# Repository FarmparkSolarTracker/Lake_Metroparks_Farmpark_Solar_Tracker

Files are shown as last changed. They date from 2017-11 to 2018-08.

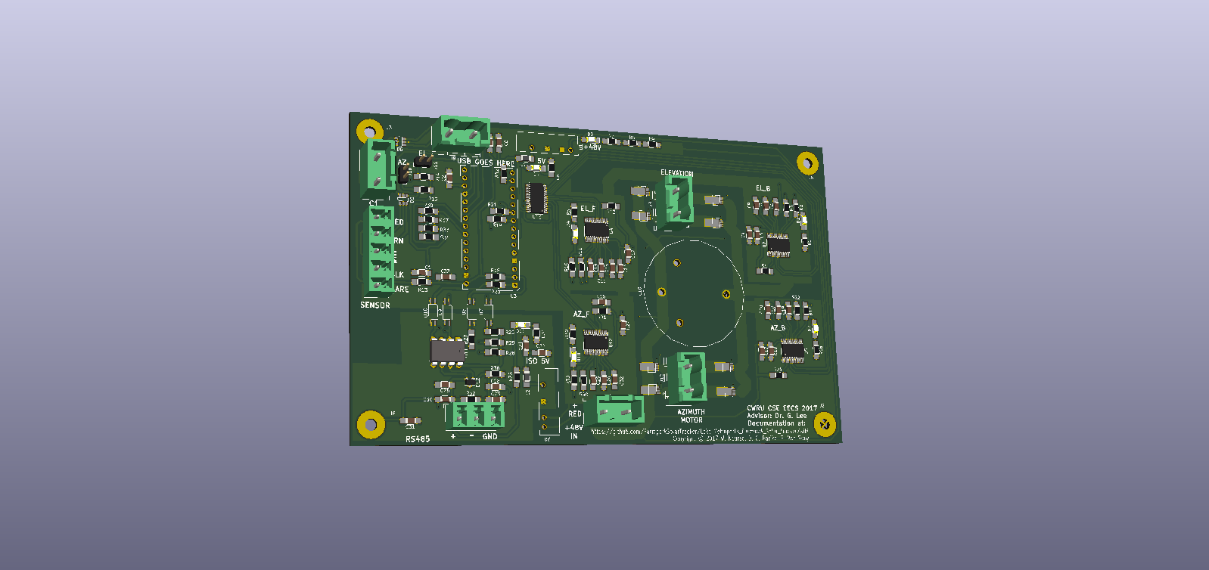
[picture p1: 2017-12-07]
Pictures/Solar_Tracker.png

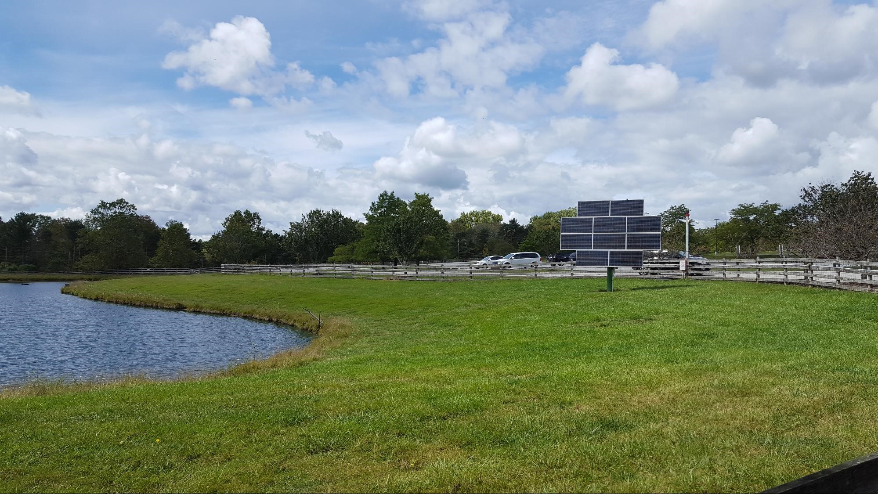
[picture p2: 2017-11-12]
Pictures/solar panel.jpg

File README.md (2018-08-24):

# Lake_Metroparks_Farmpark_Solar_Tracker
For more information, please see the wiki [here](https://github.com/FarmparkSolarTracker/Lake_Metroparks_Farmpark_Solar_Tracker/wiki).  

# Things which need work:
* Possible board issue where one side of the H-Bridges is unable to pull low, it only reaches High-Impedance
* Software for board is in a preliminary version, has not been fully tested due to the above issue
* A rough tester board has been included in the box, which theoretically can be used to send RS-485 commands to the main PCB. Code needs to be written for this device
* If the park has not done it yet, a new motor for the azimuth system must be ordered (it is believed that the worm gear is broken)
* The elevation linear actuator must be clamped in place
* Grommets must be put in place on the cables entering the new box
* Better data should be collected from the sensor, to better know how it operates

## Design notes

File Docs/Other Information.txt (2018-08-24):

Wattsun Contact Information:
	-The panel/installation model is the AZ-120
	-The two people at Watt-sun to contact are:
		-Jeff: (976)476-1256
		-Kyle: (973)647-7751
	-A replacement motor unit for the Azimuth unit was quoted to be $235, plus shipping

Drive Information:
	-I had difficulty getting the timing of the PWM expander to work with driving both the top and bottom
	of each H-Bridge, so the compromise I reached was that the bottom mosfet of the H-bridge on the appropriate
	side is held on for the duration of motion, and the corresponding top transistor is PWMed to control the 
	speed/voltage of the motor.

Preliminary Light Sensor Data:
	SIDE OF SENSOR FACING SUN | WHITE WIRE ADC | GREEN WIRE ADC
	-----------------------------------------------------------
	Middle					  | 1023           | 1023
	-----------------------------------------------------------
	Right					  | 0              | 1023
	-----------------------------------------------------------
	Left                      | 1000           | 300
	-----------------------------------------------------------
	Top                       | 600            | 1000
	-----------------------------------------------------------
	Bottom                    | 1000           | 0

Sensor schematic/pinout
	-Red: +5v in (needs a current limiting resistor)
	-Green: Middle of 2 photodiodes
	-White: Middle of other 2 photodiodes
	-Black: Ground
	-Bare: Ground for shielding

	 -------------------------------------------O +5v
	 |             |                    
	 |             | 
	___           ___
	\_/           \_/
	---           ---
	 |             |
	 |             |____________________________O Green
	 |             |                              
	 |_____________|____________________________O White
	 |             |                    
	 |             | 
	___           ___
	\_/           \_/
	---           ---
	 |             |
	 -------------------------------------------O Black

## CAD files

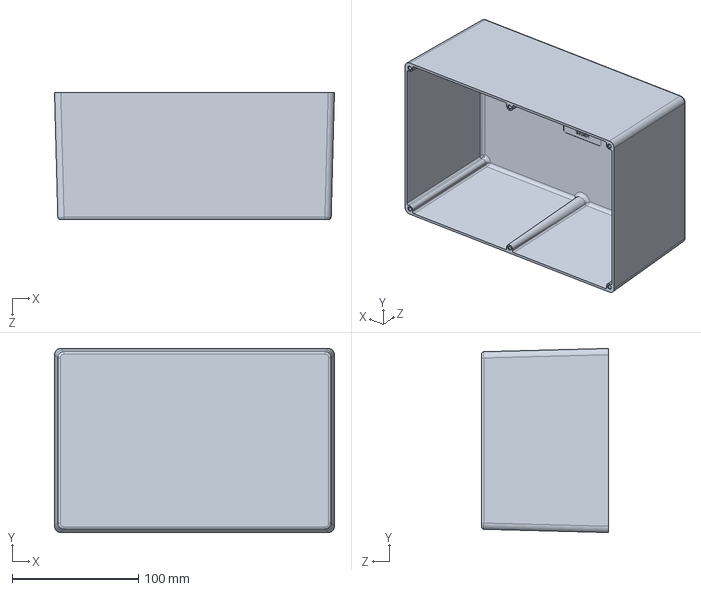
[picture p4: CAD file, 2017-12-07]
SOLIDWORKS/HM-1220-ND Box.SLDPRT
222.0 x 146.0 x 101.0 mm

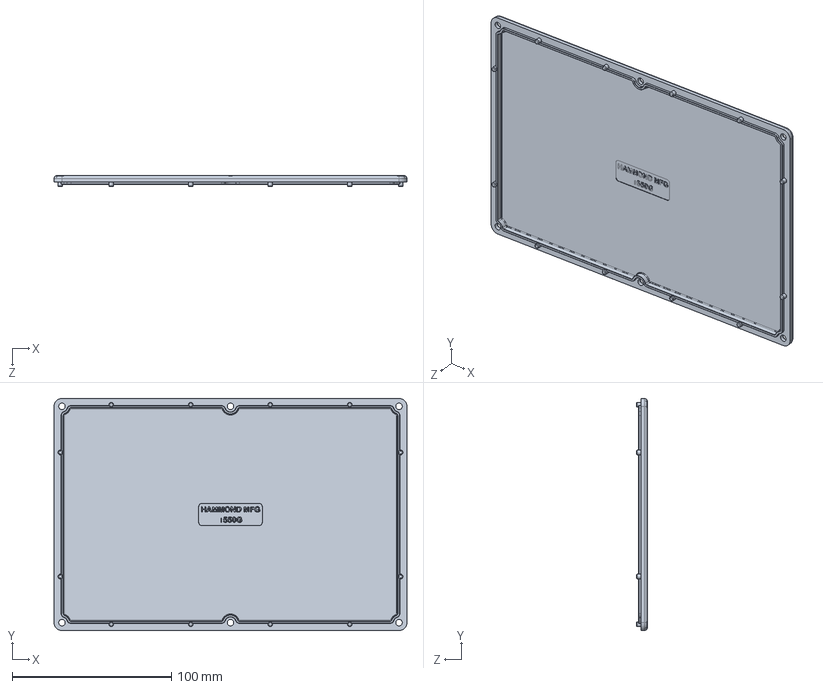
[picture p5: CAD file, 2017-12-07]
SOLIDWORKS/HM-1220-ND Lid.SLDPRT
222.0 x 146.0 x 7.00 mm

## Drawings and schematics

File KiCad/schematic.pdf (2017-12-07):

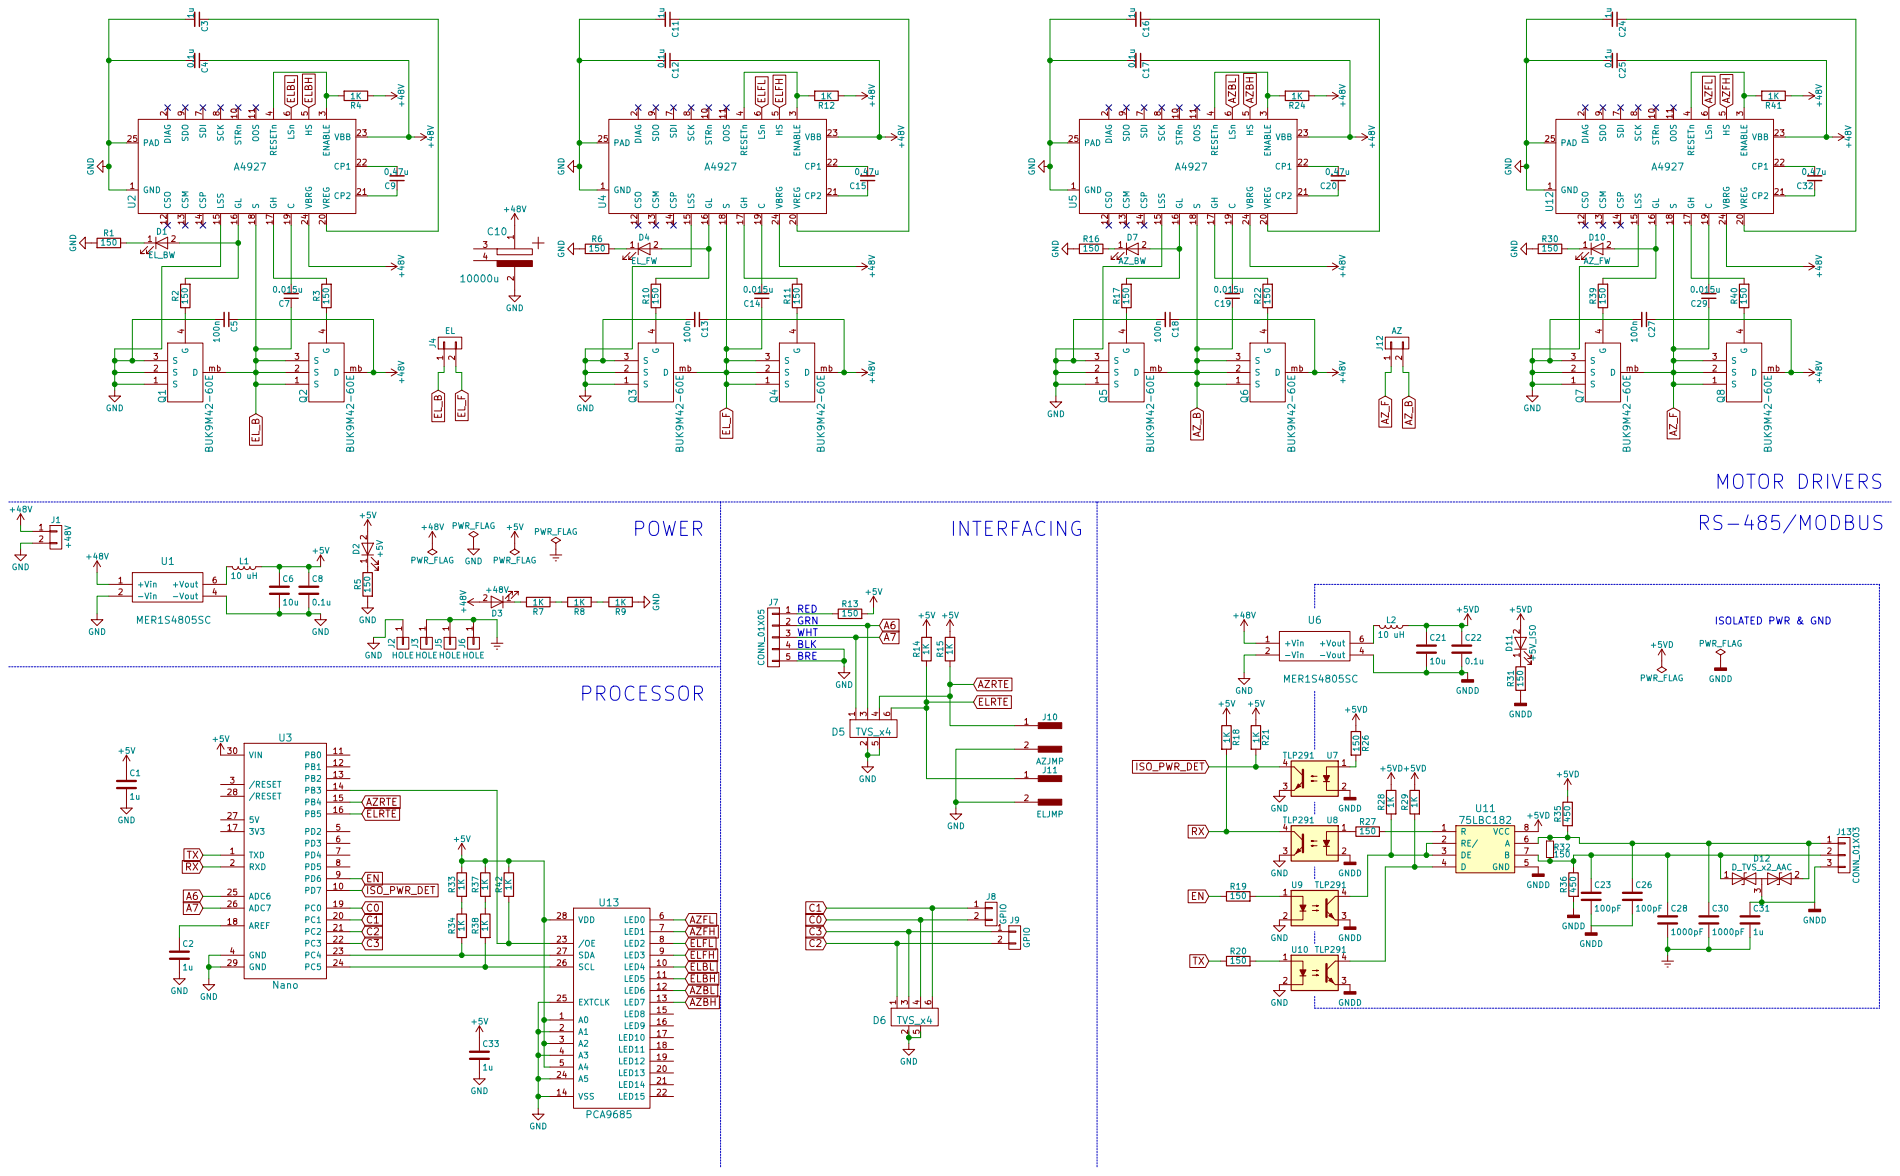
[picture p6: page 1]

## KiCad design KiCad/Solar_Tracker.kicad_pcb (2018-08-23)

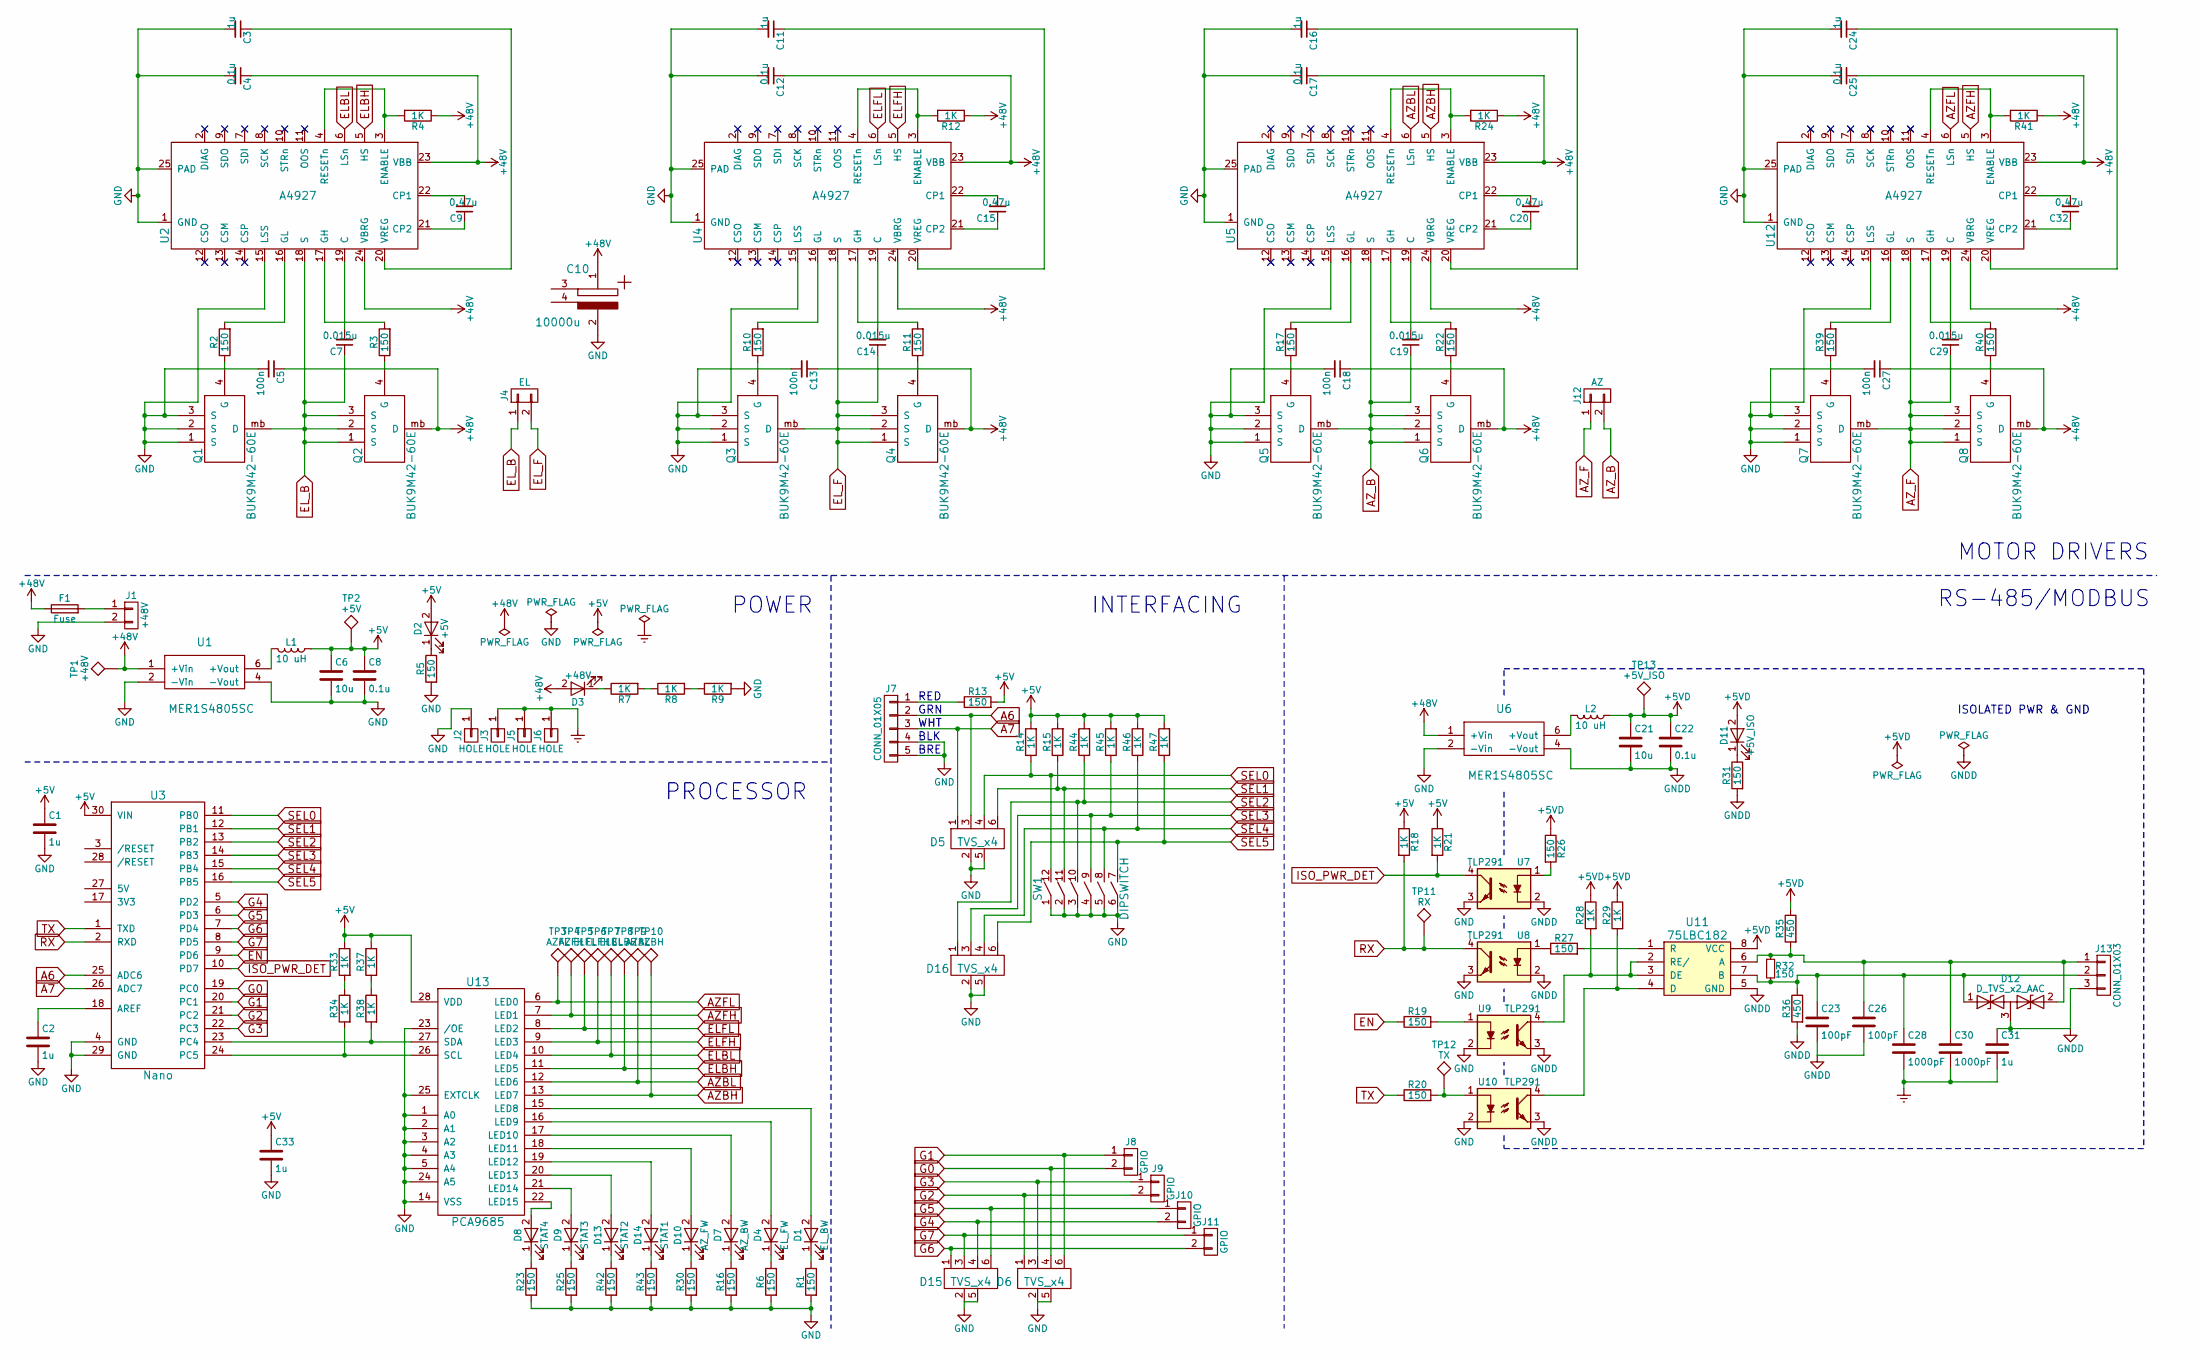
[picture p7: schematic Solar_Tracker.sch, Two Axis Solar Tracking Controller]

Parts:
C1, C2, C3, C11, C16, C24, C31, C33: 1u; C_0805
C4, C8, C12, C17, C22, C25: 0.1u; C_0805
C5, C13, C18, C27: 100n; C_0805
C6, C21: 10u; C_0805
C7, C14, C19, C29: 0.015u; C_0805
C9, C15, C20, C32: 0.47u; C_0805
C10: 10000u; vnd_cap
C23, C26: 100pF; C_0805
C28, C30: 1000pF; C_0805
D1: EL_BW; LED_1206_HandSoldering
D2: +5V; LED_1206_HandSoldering
D3: +48V; LED_1206_HandSoldering
D4: EL_FW; LED_1206_HandSoldering
D5, D6, D15, D16: TVS_x4; tvs_quad
D7: AZ_BW; LED_1206_HandSoldering
D8: STAT4; LED_1206_HandSoldering
D9: STAT3; LED_1206_HandSoldering
D10: AZ_FW; LED_1206_HandSoldering
D11: +5V_ISO; LED_1206_HandSoldering
D12: D_TVS_x2_AAC; SOT-23
D13: STAT2; LED_1206_HandSoldering
D14: STAT1; LED_1206_HandSoldering
F1: Fuse; R_Axial_DIN0204_L3.6mm_D1.6mm_P5.08mm_Horizontal
J1: +48V; PhoenixContact_GMSTBVA-G_02x7.50mm_Vertical
J2, J3, J5, J6: HOLE; M3
J4: EL; PhoenixContact_GMSTBVA-G_02x7.50mm_Vertical
J7: CONN_01X05; PhoenixContact_MCV-G_05x5.08mm_Vertical
J8, J9, J10, J11: GPIO; PhoenixContact_GMSTBVA-G_02x7.50mm_Vertical
J12: AZ; PhoenixContact_GMSTBVA-G_02x7.50mm_Vertical
J13: CONN_01X03; PhoenixContact_MCV-G_03x5.08mm_Vertical
L1, L2: 10 uH; L_1206_HandSoldering
Q1, Q2, Q3, Q4, Q5, Q6, Q7, Q8: BUK9M42-60E; nFET
R1, R2, R3, R5, R6, R10, R11, R13, R16, R17, R19, R20, R22, R23, R25, R26, R27, R30, R31, R32, R39, R40, R42, R43: 150; R_0805
R4, R7, R8, R9, R12, R14, R15, R18, R21, R24, R28, R29, R33, R34, R37, R38, R41, R44, R45, R46, R47: 1K; R_0805
R35, R36: 450; R_0805
SW1: DIPSWITCH; DIP-12_W7.62mm
TP1: +48V; test_pad
TP2: +5V; test_pad
TP3: AZFL; test_pad
TP4: AZFH; test_pad
TP5: ELFL; test_pad
TP6: ELFH; test_pad
TP7: ELBL; test_pad
TP8: ELBH; test_pad
TP9: AZBL; test_pad
TP10: AZBH; test_pad
TP11: RX; test_pad
TP12: TX; test_pad
TP13: +5V_ISO; test_pad
U1, U6: MER1S4805SC; 5v_iso
U2, U4, U5, U12: A4927; TSSOP-24_4.4x7.8mm_Pitch0.65mm
U3: Nano; Arduino_Nano
U7, U8, U9, U10: TLP291; opto
U11: 75LBC182; DIP-8_W7.62mm
U13: PCA9685; TSSOP-28_4.4x9.7mm_Pitch0.65mm

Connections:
+5V: C1.1, C6.1, C8.1, C33.1, D2.2 (A), L1.1, R13.2, R14.2, R15.2, R18.1, R21.1, R33.1, R37.1, R44.2, R45.2, R46.2, R47.2, TP2.1, U3.30 (VIN), U13.28 (VDD)
+5VD: C21.1, C22.1, D11.2 (A), L2.1, R26.1, R28.1, R29.1, R35.1, TP13.1, U11.8 (VCC)
+48V: C4.1, C5.1, C10.1, C12.1, C13.1, C17.1, C18.1, C25.1, C27.1, D3.2 (A), F1.1, Q2.mb (D), Q4.mb (D), Q6.mb (D), Q8.mb (D), R4.1, R12.1, R24.1, R41.1, TP1.1, U1.1 (+Vin), U2.23 (VBB), U2.24 (VBRG), U4.23 (VBB), U4.24 (VBRG), U5.23 (VBB), U5.24 (VBRG), U6.1 (+Vin), U12.23 (VBB), U12.24 (VBRG)
A6: D5.3, J7.2, U3.25 (ADC6)
A7: D5.1, J7.3, U3.26 (ADC7)
AZBH: TP10.1, U5.5 (HS), U13.13 (LED7)
AZBL: TP9.1, U5.6 (LSn), U13.12 (LED6)
AZFH: TP4.1, U12.5 (HS), U13.7 (LED1)
AZFL: TP3.1, U12.6 (LSn), U13.6 (LED0)
AZ_B: C19.1, J12.2, Q5.mb (D), Q6.1 (S), Q6.2 (S), Q6.3 (S), U5.18 (S)
AZ_F: C29.1, J12.1, Q7.mb (D), Q8.1 (S), Q8.2 (S), Q8.3 (S), U12.18 (S)
ELBH: TP8.1, U2.5 (HS), U13.11 (LED5)
ELBL: TP7.1, U2.6 (LSn), U13.10 (LED4)
ELFH: TP6.1, U4.5 (HS), U13.9 (LED3)
ELFL: TP5.1, U4.6 (LSn), U13.8 (LED2)
EL_B: C7.1, J4.1, Q1.mb (D), Q2.1 (S), Q2.2 (S), Q2.3 (S), U2.18 (S)
EL_F: C14.1, J4.2, Q3.mb (D), Q4.1 (S), Q4.2 (S), Q4.3 (S), U4.18 (S)
EN: R19.1, U3.9 (PD6)
Earth: C28.2, C30.2, C31.2, J3.1, J5.1, J6.1
G0: D6.4, J8.2, U3.19 (PC0)
G1: D6.6, J8.1, U3.20 (PC1)
G2: D6.1, J9.2, U3.21 (PC2)
G3: D6.3, J9.1, U3.22 (PC3)
G4: D15.4, J10.2, U3.5 (PD2)
G5: D15.6, J10.1, U3.6 (PD3)
G6: D15.1, J11.2, U3.7 (PD4)
G7: D15.3, J11.1, U3.8 (PD5)
GND: C1.2, C2.2, C3.2, C4.2, C5.2, C6.2, C8.2, C10.2, C11.2, C12.2, C13.2, C16.2, C17.2, C18.2, C24.2, C25.2, C27.2, C33.2, D5.2, D5.5, D6.2, D6.5, D15.2, D15.5, D16.2, D16.5, J1.2, J2.1, J7.4, J7.5, Q1.1 (S), Q1.2 (S), Q1.3 (S), Q3.1 (S), Q3.2 (S), Q3.3 (S), Q5.1 (S), Q5.2 (S), Q5.3 (S), Q7.1 (S), Q7.2 (S), Q7.3 (S), R1.2, R5.2, R6.2, R9.2, R16.2, R23.2, R25.2, R30.2, R42.2, R43.2, SW1.1, SW1.2, SW1.3, SW1.4, SW1.5, SW1.6, U1.2 (-Vin), U1.4 (-Vout), U2.1 (GND), U2.15 (LSS), U2.25 (PAD), U3.4 (GND), U3.29 (GND), U4.1 (GND), U4.15 (LSS), U4.25 (PAD), U5.1 (GND), U5.15 (LSS), U5.25 (PAD), U6.2 (-Vin), U7.3, U8.3, U9.2, U10.2, U12.1 (GND), U12.15 (LSS), U12.25 (PAD), U13.1 (A0), U13.2 (A1), U13.3 (A2), U13.4 (A3), U13.5 (A4), U13.14 (VSS), U13.23 (/OE), U13.24 (A5), U13.25 (EXTCLK)
GNDD: C21.2, C22.2, C23.2, C26.2, C31.1, D12.3 (common), J13.3, R31.2, R36.2, U6.4 (-Vout), U7.2, U8.2, U9.3, U10.3, U11.5 (GND)
ISO_PWR_DET: R21.2, U3.10 (PD7), U7.4
unnamed: C2.1, U3.18 (AREF)
unnamed: C3.1, U2.20 (VREG)
unnamed: C7.2, U2.19 (C)
unnamed: C9.1, U2.21 (CP2)
unnamed: C9.2, U2.22 (CP1)
unnamed: C11.1, U4.20 (VREG)
unnamed: C14.2, U4.19 (C)
unnamed: C15.1, U4.21 (CP2)
unnamed: C15.2, U4.22 (CP1)
unnamed: C16.1, U5.20 (VREG)
unnamed: C19.2, U5.19 (C)
unnamed: C20.1, U5.21 (CP2)
unnamed: C20.2, U5.22 (CP1)
unnamed: C23.1, C28.1, D12.1 (A1), J13.2, R32.2, R36.1, U11.7 (B)
unnamed: C24.1, U12.20 (VREG)
unnamed: C26.1, C30.1, D12.2 (A2), J13.1, R32.1, R35.2, U11.6 (A)
unnamed: C29.2, U12.19 (C)
unnamed: C32.1, U12.21 (CP2)
unnamed: C32.2, U12.22 (CP1)
unnamed: D1.1 (K), R1.1
unnamed: D1.2 (A), U13.15 (LED8)
unnamed: D2.1 (K), R5.1
unnamed: D3.1 (K), R7.1
unnamed: D4.1 (K), R6.1
unnamed: D4.2 (A), U13.16 (LED9)
unnamed: D7.1 (K), R16.1
unnamed: D7.2 (A), U13.17 (LED10)
unnamed: D8.1 (K), R23.1
unnamed: D8.2 (A), U13.22 (LED15)
unnamed: D9.1 (K), R25.1
unnamed: D9.2 (A), U13.21 (LED14)
unnamed: D10.1 (K), R30.1
unnamed: D10.2 (A), U13.18 (LED11)
unnamed: D11.1 (K), R31.1
unnamed: D13.1 (K), R42.1
unnamed: D13.2 (A), U13.20 (LED13)
unnamed: D14.1 (K), R43.1
unnamed: D14.2 (A), U13.19 (LED12)
unnamed: F1.2, J1.1
unnamed: J7.1, R13.1
unnamed: L1.2, U1.6 (+Vout)
unnamed: L2.2, U6.6 (+Vout)
unnamed: Q1.4 (G), R2.1
unnamed: Q2.4 (G), R3.1
unnamed: Q3.4 (G), R10.1
unnamed: Q4.4 (G), R11.1
unnamed: Q5.4 (G), R17.1
unnamed: Q6.4 (G), R22.1
unnamed: Q7.4 (G), R39.1
unnamed: Q8.4 (G), R40.1
unnamed: R2.2, U2.16 (GL)
unnamed: R3.2, U2.17 (GH)
unnamed: R4.2, U2.3 (ENABLE), U2.4 (RESETn)
unnamed: R7.2, R8.1
unnamed: R8.2, R9.1
unnamed: R10.2, U4.16 (GL)
unnamed: R11.2, U4.17 (GH)
unnamed: R12.2, U4.3 (ENABLE), U4.4 (RESETn)
unnamed: R17.2, U5.16 (GL)
unnamed: R19.2, U9.1
unnamed: R20.2, TP12.1, U10.1
unnamed: R22.2, U5.17 (GH)
unnamed: R24.2, U5.3 (ENABLE), U5.4 (RESETn)
unnamed: R26.2, U7.1
unnamed: R27.1, U8.1
unnamed: R27.2, U11.1 (R)
unnamed: R28.2, U9.4, U11.2 (RE/), U11.3 (DE)
unnamed: R29.2, U10.4, U11.4 (D)
unnamed: R33.2, R34.1
unnamed: R34.2, U3.24 (PC5), U13.26 (SCL)
unnamed: R37.2, R38.1
unnamed: R38.2, U3.23 (PC4), U13.27 (SDA)
unnamed: R39.2, U12.16 (GL)
unnamed: R40.2, U12.17 (GH)
unnamed: R41.2, U12.3 (ENABLE), U12.4 (RESETn)
RX: R18.2, TP11.1, U3.2 (RXD), U8.4
SEL0: D5.4, R14.1, SW1.12, U3.11 (PB0)
SEL1: D5.6, R15.1, SW1.11, U3.12 (PB1)
SEL2: D16.1, R44.1, SW1.10, U3.13 (PB2)
SEL3: D16.3, R45.1, SW1.9, U3.14 (PB3)
SEL4: D16.4, R46.1, SW1.8, U3.15 (PB4)
SEL5: D16.6, R47.1, SW1.7, U3.16 (PB5)
TX: R20.1, U3.1 (TXD)

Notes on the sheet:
ISOLATED PWR & GND
POWER
PROCESSOR
INTERFACING
RS-485/MODBUS
MOTOR DRIVERS
RED
GRN
WHT
BLK
BRE

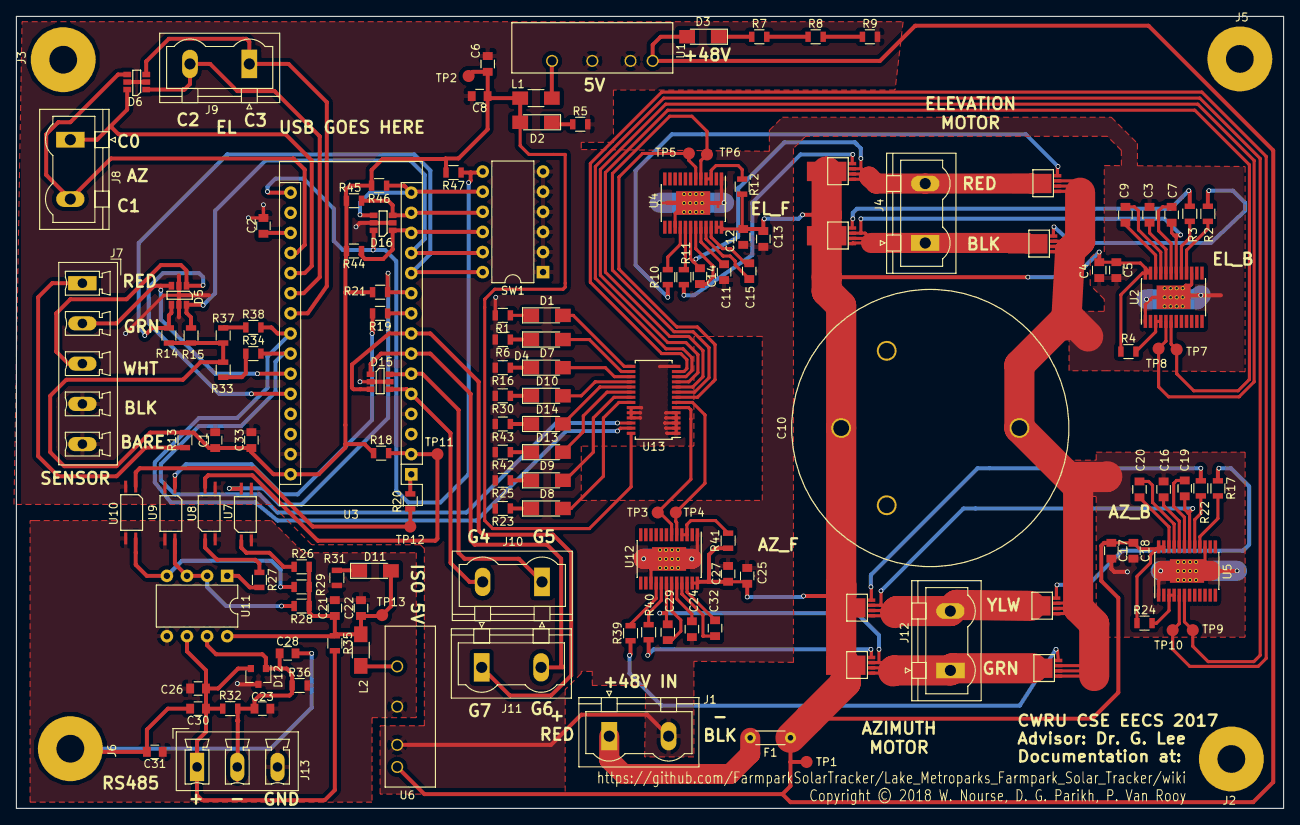
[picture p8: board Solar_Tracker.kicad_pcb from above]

Board: 2 copper layers, 160.0 x 100.0 mm, 147 parts (0 on the bottom side), 113 nets.

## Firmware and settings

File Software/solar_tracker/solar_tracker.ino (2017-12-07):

/*
 * Farmpark Solar Tracker
 * © William Nourse, Darshan G. Parikh, Paula Van Rooy 2017
 */

#include <Adafruit_PWMServoDriver.h>
#include <ModbusSerial.h>
#include <Modbus.h>
#include <Servo.h>
#include <Wire.h>

Adafruit_PWMServoDriver pwm = Adafruit_PWMServoDriver();
//Flags
boolean rs485 = false;    //has rs485 data been received?
boolean balanced = false; //is the system lined up with the sun?
boolean azimuth = false;  //does the azimuth need adjusted?
boolean night = false;    //is it nighttime?

byte override = 0x00; //register for button presses(bang-bang)

//Variables
int az_scale = 1;   //scaling factor for azimuth PWM
int el_scale = 1;   //scaling factor for elevation PWM
int pin_state = 0;  //holder variable for digitalRead operations
int pin_state1 = 0; //holder variable for digitalRead operations (bang-bang)
int pin_state2 = 0; //holder variable for digitalRead operations (bang-bang)
int pin_state3 = 0; //holder variable for digitalRead operations (bang-bang)
int pin_state4 = 0; //holder variable for digitalRead operations (bang-bang)
int command = 0;    //velocity which will be sent to the motor
int el_cp = 0;      //output of elevation positional controller
int az_cp = 0;      //output of azimuth positional controller
int v = 0;          //override duty cycle
int az_store = 0;   //holder variable for azimuth sensor reading (bang-bang)
int el_store = 0;   //holder variable for elevation senseor reading (bang-bang)
int wait = 0;       //counter for pausing after an override
unsigned int idle = 0;  //counter for determining if it is nighttime

//Balance thresholds
const int THRESH_L = 100;
const int THRESH_H = 200;

//Configuration jumpers
const int AZRTE = 12;
const int ELRTE = 13;

//GPIO Pins
const int C0 = 14;
const int C1 = 15;
const int C2 = 16;
const int C3 = 17;

//Isolated Interface
const int ISO_PWR_DET = 7;
const int TXRX_ENABLE = 6;

//Motor Pins
const int EL_BL = 8;
const int EL_BH = 9;
const int EL_FL = 4;
const int EL_FH = 5;
const int AZ_BL = 10;
const int AZ_BH = 11;
const int AZ_FL = 2;
const int AZ_FH = 3;

//Sensor Pins
const int EL_SENSE = A6;
const int AZ_SENSE = A7;


//Modbus Register Offsets (0-9999)

//Modbus Input Registers (Master Read-Only)
const int SENSOR_AZ_IREG = 1001;
const int SENSOR_EL_IREG = 1111;

//Modbus Holding Registers (Master Read/Write)
const int OVERRIDE_HREG = 111;

//ModbusSerial object
ModbusSerial mb;

void setup() {
  
  //Modbus Setup//////////////////////////

  //Config Modbus Serial (port, speed, byte format)
  mb.config(& Serial, 38400, TXRX_ENABLE); //Check on how to enable enable pin
  //Set the Slave ID (1-247)
  mb.setSlaveId(212);

  //Add Input Registers
  mb.addIreg(SENSOR_AZ_IREG);
  mb.addIreg(SENSOR_EL_IREG);
  //Add Holding Registers
  mb.addHreg(OVERRIDE_HREG, 0);

  //Pinmodes/////////////////////////////
  pinMode(TXRX_ENABLE, OUTPUT);
  pinMode(EL_BL, OUTPUT);
  pinMode(EL_BH, OUTPUT);
  pinMode(EL_FL, OUTPUT);
  pinMode(EL_FH, OUTPUT);
  pinMode(AZ_BL, OUTPUT);
  pinMode(AZ_BH, OUTPUT);
  pinMode(AZ_FL, OUTPUT);
  pinMode(AZ_FH, OUTPUT);
  
  pinMode(AZRTE, INPUT);
  pinMode(ELRTE, INPUT);
  pinMode(ISO_PWR_DET, INPUT);
  pinMode(C0, INPUT);
  pinMode(C1, INPUT);
  pinMode(C2, INPUT);
  pinMode(C3, INPUT);  

  //Serial.begin(9600);
  //Initialization/////////////////////

  //Set scaling factors
  pin_state = digitalRead(AZRTE);
  if (pin_state == LOW){
    az_scale = 2;
  }
  pin_state = digitalRead(ELRTE);
  if (pin_state == LOW){
    el_scale = 2;
  }

  //Wait until isolated section has fully powered on before starting
  pin_state = digitalRead(ISO_PWR_DET);
  while (pin_state == HIGH){
    pin_state = digitalRead(ISO_PWR_DET);
  }

  pwm.begin();

  pwm.setPWMFreq(60);

  yield();
}

void loop() {
  //Check 485////////////////////////
  //mb.task();
  //Read buttons (bang-bang)
  pin_state1 = digitalRead(C0);
  pin_state2 = digitalRead(C1);
  pin_state3 = digitalRead(C2);
  pin_state4 = digitalRead(C3);
  if (pin_state1 == HIGH){
    override = B00000001;
    // Serial.print("Override = ");
    //Serial.println(override);
  }else if (pin_state2 == HIGH){
    override = B00000010;
    // Serial.print("Override = ");
    //Serial.println(override);
  }else if (pin_state3 == HIGH){
    override = B00000100;
    //Serial.print("Override = ");
    //Serial.println(override);
  }else if (pin_state4 == HIGH){
    override = B00001000;
     //Serial.print("Override = ");
    //Serial.println(override);
  }else{
    override = 0x00;
     //Serial.print("Override = ");
    //Serial.println(override);
  }
  
  //Check override register(bang-bang)
  if (override == 0){
    if (rs485 == true){
      if (wait == 255){
        wait = 0;
        rs485 = false;
      }else{
        wait++;
        //Serial.print("Wait = ");
        //Serial.println(wait);
      }
    }
  }else{
    rs485 = true;
    wait = 0;
    switch(override){
      case B00000001:
        azimuth = false;
        v = 4095;
        break;
      case B00000010:
        azimuth = false;
        v = -4095;
        break;
      case B00000100:
        azimuth = true;
        v = 4095;
        break;
      case B00001000:
        azimuth = true;
        v = -4095;
        break;
      default:
        azimuth = false;
        v = 0;
        break;
    }
  }
/*
  //Determine if night//////////////////
  if(balanced == true){
    if(idle == 65500){
      if(night == false){
        night = true;
        //stop elevation motor
        digitalWrite(EL_BH, LOW);
        digitalWrite(EL_FH, LOW);
        digitalWrite(EL_BL, LOW);
        digitalWrite(EL_FL, LOW);
        //move azimuth fast east
        digitalWrite(AZ_BH, LOW);
        digitalWrite(AZ_FL,HIGH);
        digitalWrite(AZ_BL,LOW);
        analogWrite(AZ_FH,255/az_scale);
        delay(15000); //delay 15 seconds
        //stop azimuth
        digitalWrite(AZ_BH, LOW);
        digitalWrite(AZ_FH, LOW);
        digitalWrite(AZ_BL, LOW);
        digitalWrite(AZ_FL, LOW);
      }
    }
  }else{
    idle = 0;
    night = false;
  }
*/
  //control loop///////////////////////////
  for(int i=0; i<100; i++){
  //Input multiplexer////////////////////
    if (rs485 == true){
      command = v;
      //Serial.println("comm = v");
    }else{
      command = 0;
      //Serial.println("comm = 0");
    }

    /*if (rs485 == true){
      command = v;
      //Serial.println("comm = v");
    }else{
      if(azimuth == true){
        command = az_cp;
      }else{
        command = el_cp;
      }
      command = 0;
      //Serial.println("comm = 0");
    }*/

    //Sensor//////////////////////////////
    mb.Ireg(SENSOR_AZ_IREG, analogRead(AZ_SENSE));
    mb.Ireg(SENSOR_EL_IREG, analogRead(EL_SENSE));
    if((mb.Ireg(SENSOR_AZ_IREG) >= THRESH_L) && (mb.Ireg(SENSOR_AZ_IREG) < THRESH_H)){
       azimuth = false;
      if((mb.Ireg(SENSOR_EL_IREG) >= THRESH_L) && (mb.Ireg(SENSOR_EL_IREG) < THRESH_H)){
        balanced = true;
        az_cp = 0;
        el_cp = 0;
      }else{
        balanced = false;
        az_cp = 0;
        //ctrl_pos(2,T-el);
      }
    
    /*
    az_store = analogRead(AZ_SENSE);
    el_store = analogRead(EL_SENSE);
    if((az_store >= THRESH_L) && (az_store < THRESH_H)){
      azimuth = false;
      if((el_store >= THRESH_L) && (el_store < THRESH_H)){
        balanced = true;
        //ctrl_pos(1,0);
        //ctrl_pos(2,0);
      }else{
        balanced = false;
        //ctrl_pos(1,0);
        //ctrl_pos(2,T-el)
      }
    }else{
      balanced = false;
      //ctrl_pos(2,0);
      //ctrl_pos(1,T-az);
      azimuth = true;
    }*/
    }else{
      balanced = false;
      el_cp = 0;
      //az_cp = something;
      azimuth = true;
    }
  }
  
  //Output demultiplexer//////////////
  if(azimuth == true){
    //stop elevation
    digitalWrite(EL_BH, LOW);
    digitalWrite(EL_FH, LOW);
    digitalWrite(EL_BL, LOW);
    digitalWrite(EL_FL, LOW);
    //Serial.println("stop el");
    if(command >= 0){
      //move azimuth east
      digitalWrite(AZ_BH, LOW);
      digitalWrite(AZ_FL,HIGH);
      digitalWrite(AZ_BL,LOW);
      analogWrite(AZ_FH,command/az_scale);
      
      //Serial.println("az east");
      //Serial.print("comm = ");
      //Serial.println(command);
    }else{
      //move azimuth west
      digitalWrite(AZ_FH,LOW);
      digitalWrite(AZ_BL,HIGH);
      digitalWrite(AZ_FL,LOW);
      analogWrite(AZ_BH,abs(command)/az_scale);
    
      //Serial.println("az west");
      //Serial.print("comm = ");
      //Serial.println(command);
    }
  }else{
    //stop azimuth
    digitalWrite(AZ_BH, LOW);
    digitalWrite(AZ_FH, LOW);
    digitalWrite(AZ_BL, LOW);
    digitalWrite(AZ_FL, LOW);
    //Serial.println("stop az");
    if(command >= 0){
      //move elevation up
      digitalWrite(EL_BH, LOW);
      digitalWrite(EL_FL,HIGH);
      digitalWrite(EL_BL,LOW);
      analogWrite(EL_FH,command/el_scale);
      //Serial.println("el up");
      //Serial.print("comm = ");
      //Serial.println(command);
    }else{
      //move elevation down
      digitalWrite(EL_FH,LOW);
      digitalWrite(EL_BL,HIGH);
      digitalWrite(EL_FL,LOW);
      analogWrite(EL_BH,abs(command)/el_scale);
      //Serial.println("el down");
      //Serial.print("comm = ");
      //Serial.println(command);
    }
  }
}

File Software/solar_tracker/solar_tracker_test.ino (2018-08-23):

#include <Wire.h>

/*
 * Farmpark Solar Tracker
 * © William Nourse, Darshan G. Parikh, Paula Van Rooy 2017
 */
#include <Adafruit_PWMServoDriver.h>

//declare pwm driver object
Adafruit_PWMServoDriver pwm = Adafruit_PWMServoDriver();

//expander pin numbers of motor drivers
int AZ_FL = 0;
int AZ_FH = 1;
int AZ_BL = 6;
int AZ_BH = 7;
int EL_FL = 2;
int EL_FH = 3;
int EL_BL = 4;
int EL_BH = 5;

//expander pin numbers of LEDs
int LED_ELB = 8;
int LED_ELF = 9;
int LED_AZB = 10;
int LED_AZF = 11;
int LED_ST1 = 12;
int LED_ST2 = 13;
int LED_ST3 = 14;
int LED_ST4 = 15;

//config switch pins
int SEL0 = 8;
int SEL1 = 9;
int SEL2 = 10;
int SEL3 = 11;
int SEL4 = 12;
int SEL5 = 13;

//speed temp variables
int az36 = 0;
int az48 = 0;
int el36 = 0;
int el48 = 0;

int azSpeed = 2048;
int azNeg = 2048;
int elSpeed = 2048;
int elNeg = 2048;

void setup() {
  //initialize expander communication
  pwm.begin();
  pwm.setPWMFreq(60); //Hz

  //Pinmodes
  pinMode(SEL0, INPUT);
  pinMode(SEL1, INPUT);
  pinMode(SEL2, INPUT);
  pinMode(SEL3, INPUT);
  pinMode(SEL4, INPUT);
  pinMode(SEL5, INPUT);

  az36 = digitalRead(SEL0);
  az48 = digitalRead(SEL1);
  el36 = digitalRead(SEL2);
  el48 = digitalRead(SEL4);

  //Set azimuth motor scaling from switches
  if (az48 == HIGH){
    azSpeed = 4096;
    pwm.setPWM(LED_ST1,4096,0);
  }else if (az36 == HIGH){
    azSpeed = 3072;
    pwm.setPWM(LED_ST2,4096,0);
  }else{
    azSpeed = 2048;
  }
  //Set elevation motor scaling from switches
  if (el48 == HIGH){
    elSpeed = 4096;
    pwm.setPWM(LED_ST3,4096,0);
  }else if (el36 == HIGH){
    elSpeed = 3072;
    pwm.setPWM(LED_ST4,4096,0);
  }else{
    elSpeed = 2048;
  }
  azNeg = 4096 - azSpeed;
  elNeg = 4096 - elSpeed;

}

void loop() {
  ctrlMotor(false,true);  //el_fw light, jack shit
  ctrlMotor(true,true);  //az_fw light, jack shit
  delay(1000);
  //freezeMotor();
  //delay(1000);
  //ctrlMotor(true,false);  //az_bw light, az_bw drive
  //ctrlMotor(false,false); //el_bw light, el_bw drive
  //delay(1000);
  freezeMotor();
  //freezeMotor();
  delay(1000);
}

void ctrlMotor(bool az, bool fwd){
  if (az == true){
    if (fwd == true){
      pwm.setPWM(AZ_FH,azSpeed,azNeg);
      pwm.setPWM(LED_AZF,azSpeed,azNeg);
      pwm.setPWM(AZ_FL,4096,0);
      pwm.setPWM(AZ_BH,0,4096);
      pwm.setPWM(AZ_BL,0,4096);
    }else{
      pwm.setPWM(AZ_FH,0,4096);
      pwm.setPWM(AZ_FL,0,4096);
      pwm.setPWM(AZ_BH,azSpeed,azNeg);
      pwm.setPWM(LED_AZB,azSpeed,azNeg);
      pwm.setPWM(AZ_BL,4096,0);
    }
  }else{
    if (fwd == true){
      pwm.setPWM(EL_FH,elSpeed,elNeg);
      pwm.setPWM(LED_ELF,elSpeed,elNeg);
      pwm.setPWM(EL_FL,4096,0);
      pwm.setPWM(EL_BH,0,4096);
      pwm.setPWM(EL_BL,0,4096);
    }else{
      pwm.setPWM(EL_FH,0,4096);
      pwm.setPWM(EL_FL,0,4096);
      pwm.setPWM(EL_BH,elSpeed,elNeg);
      pwm.setPWM(LED_ELB,elSpeed,elNeg);
      pwm.setPWM(EL_BL,4096,0);
    }
  }
}

void freezeMotor(){
    pwm.setPWM(AZ_FH,0,4096);
    pwm.setPWM(AZ_FL,0,4096);
    pwm.setPWM(AZ_BH,0,4096);
    pwm.setPWM(AZ_BL,0,4096);
    pwm.setPWM(LED_AZF,0,4096);
    pwm.setPWM(LED_AZB,0,4096);
    pwm.setPWM(EL_FH,0,4096);
    pwm.setPWM(EL_FL,0,4096);
    pwm.setPWM(EL_BH,0,4096);
    pwm.setPWM(EL_BL,0,4096);
    pwm.setPWM(LED_ELF,0,4096);
    pwm.setPWM(LED_ELB,0,4096);
}

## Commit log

2017-09-09 Started work on schematic
    [Solar_Tracker.kicad_pcb, Solar_Tracker.sch]
2017-09-17 Replaced optos and bus transceiver with through-hole versions
    [Solar_Tracker.sch]
2017-09-21 Added FTDI chip to library, added Atmega328 to schematic
    [Solar_Tracker.sch]
2017-09-21 added connections to FTDI chip
    [Solar_Tracker.sch]
2017-09-22 made the schematic
    [Solar_Tracker.sch]
2017-09-22 Paula's Changes
    [Solar_Tracker.sch, _saved_Solar_Tracker.sch]
2017-09-22 Paula's update for power
    [Solar_Tracker.sch, _saved_Solar_Tracker.sch]
2017-09-22 Update to add symbol 32U4 to schematic
    [Solar_Tracker.sch]
2017-09-22 Added isolation marking for RS-485
    [Solar_Tracker.sch]
2017-09-22 Added USB hardware to ATMEGA32u4 symbol
    [Solar_Tracker.sch]
2017-09-22 Added power connections and bypass caps to 32u4
    [Solar_Tracker.sch]
2017-09-22 Added all port names for 32u4
    [Solar_Tracker.sch]
2017-09-23 Set resistor values, added status LEDs, and added resonator
    [Solar_Tracker.sch]
2017-09-23 Rearranged blocks of schematic
    [Solar_Tracker.sch]
2017-09-25 Added to library and schematic for gate drivers and H-bridges. Still need to confirm gate driver capacitor values. Also, rearranged overall schematic for neatness. May need to adjust slightly to acco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
    [Solar_Tracker.sch]
2017-09-25 Rearranged into blocks, added visual indicator lines
    [Solar_Tracker.sch]
2017-09-25 Added power flags
    [Solar_Tracker.sch]
2017-09-25 Added motor capacitors
    [Solar_Tracker.sch]
2017-09-26 Updated pullups on config jumpers
    [Solar_Tracker.sch]
2017-09-29 Redid analog connector
    [Solar_Tracker.sch]
2017-10-03 New motor cap values
    [Solar_Tracker.sch]
2017-10-03 Paired with footprints
    [Solar_Tracker.sch]
2017-10-03 Added nFET footprint
    [Solar_Tracker.sch]
2017-10-04 Changed 5v filter caps
    [Solar_Tracker.sch]
2017-10-04 Associated footprints
    [Solar_Tracker.sch]
2017-10-05 Added title block info
    [Solar_Tracker.sch]
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2017-10-05 Updated capacitor symbol in schematic, updated linkings between components and symbols
    [Solar_Tracker.sch]
2017-10-05 Added mounting hole footprint, tied to hole symbol
    [Solar_Tracker.sch]
2017-10-05 Spread out components on PCB
    [Solar_Tracker.kicad_pcb]
2017-10-05 Updated switch symbol, added nFET landings to pcb
    [Solar_Tracker.kicad_pcb]
2017-10-05 Updated symbols for TVS_USB and the motor driver
    [Solar_Tracker.kicad_pcb]
2017-10-05 All components in PCB
    [Solar_Tracker.kicad_pcb, _saved_Solar_Tracker.sch]
2017-10-06 Work on grouping components
    [Solar_Tracker.kicad_pcb, Solar_Tracker.sch, _saved_Solar_Tracker.sch]
2017-10-06 saved changes
    [Solar_Tracker.kicad_pcb]
2017-10-10 Started work on layout
    [Solar_Tracker.kicad_pcb, _saved_Solar_Tracker.sch]
2017-10-10 more layout work
    [Solar_Tracker.kicad_pcb]
2017-10-12 Layout updates
    [Solar_Tracker.kicad_pcb]
2017-10-12 Updated schematic to use Nano, added Nano part
    [Solar_Tracker.sch, _saved_Solar_Tracker.sch]
2017-10-12 Updated annotation
    [Solar_Tracker.sch]
2017-10-12 Fixing library issues
    [Solar_Tracker.sch]
2017-10-12 Added nano footprint
    [Solar_Tracker.sch]
2017-10-12 Exported netlist
    [Solar_Tracker.kicad_pcb]
2017-10-12 Updated netlist in pcb
    [Solar_Tracker.kicad_pcb, Solar_Tracker.sch]
2017-10-12 Fixed CvPCB
    [Solar_Tracker.kicad_pcb, Solar_Tracker.sch]
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2017-10-13 updates again
    [Solar_Tracker.kicad_pcb]
2017-10-13 regrouping in process
    [Solar_Tracker.kicad_pcb, _saved_Solar_Tracker.sch]
2017-10-13 all components regrouped
    [Solar_Tracker.kicad_pcb]
2017-10-13 motor work
    [Solar_Tracker.kicad_pcb]
2017-10-15 layout work
    [Solar_Tracker.kicad_pcb, _saved_Solar_Tracker.sch]
2017-10-15 interfacing/rs485 version 1 complete
    [Solar_Tracker.kicad_pcb]
2017-10-15 initial layout
    [Solar_Tracker.kicad_pcb]
2017-10-16 Layout prelim not RS-485
    [Solar_Tracker.kicad_pcb]
2017-10-17 Rearranged connectors, reassigned mounting hole power
    [Solar_Tracker.sch]
2017-10-17 Fixed connector issues
    [Solar_Tracker.kicad_pcb, Solar_Tracker.sch]
2017-10-17 motor updates
    [Solar_Tracker.kicad_pcb]
2017-10-17 Updated source connections
    [Solar_Tracker.kicad_pcb, Solar_Tracker.sch]
2017-10-17 Tuesday layout changes - motors and notes
    [Solar_Tracker.kicad_pcb]
2017-10-19 redone motor layout
    [Solar_Tracker.kicad_pcb]
2017-10-19 Version 2 layout complete
    [Solar_Tracker.kicad_pcb]
2017-10-19 Fixes for Paula
    [Solar_Tracker.kicad_pcb, Solar_Tracker.sch]
2017-10-19 Saved fixes
    [Solar_Tracker.sch]
2017-10-20 Reviewed layout with J.G. - approved
    [Solar_Tracker.kicad_pcb]
2017-10-22 Ver. 3 RS-485-done
    [Solar_Tracker.kicad_pcb]
2017-10-24 interfacing/processor Ver. 3 complete, motor in progress
    [Solar_Tracker.kicad_pcb]
2017-10-24 Fixed ground for Paula
    [Solar_Tracker.kicad_pcb, Solar_Tracker.sch]
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2017-10-25 planes and motor updates
    [Solar_Tracker.kicad_pcb]
2017-10-26 added planes and updates
    [Solar_Tracker.kicad_pcb]
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2017-10-26 made the ratsnest go away
    [Solar_Tracker.kicad_pcb]
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2017-11-12 Fixed driver footprint
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2017-11-12 Fixed connectors
    [Solar_Tracker.kicad_pcb, _saved_Solar_Tracker.sch]
2017-11-12 Added pwm expander symbol
    [Solar_Tracker.sch, _saved_Solar_Tracker.sch]
2017-11-12 Added expander to pcb
    [Solar_Tracker.kicad_pcb, _saved_Solar_Tracker.sch]
2017-11-13 updates to layout due to new footprints. Gave space to power, fixed connectors, began motors
    [Solar_Tracker.kicad_pcb]
2017-11-13 Fixed pinout for paula
    [Solar_Tracker.sch, _saved_Solar_Tracker.sch]
2017-11-13 continued with motors and new layout
    [Solar_Tracker.kicad_pcb]
2017-11-13 Updated schematic for Paula
    [Solar_Tracker.sch]
2017-11-13 Same stuff, different day
    [Solar_Tracker.kicad_pcb, Solar_Tracker.sch]
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

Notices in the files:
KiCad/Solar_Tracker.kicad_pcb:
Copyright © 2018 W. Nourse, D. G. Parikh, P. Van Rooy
